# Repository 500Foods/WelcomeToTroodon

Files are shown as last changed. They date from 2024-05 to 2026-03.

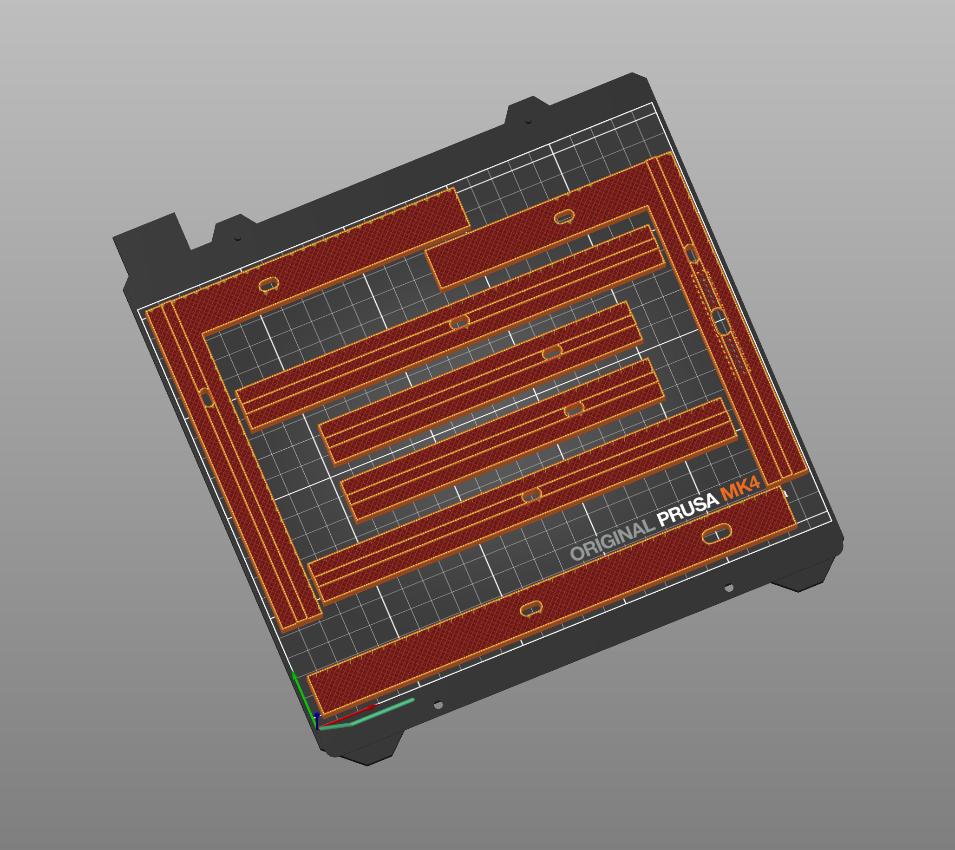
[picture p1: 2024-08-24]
3D_Files/RearPanelInserts/RearPanelInserts-01.png

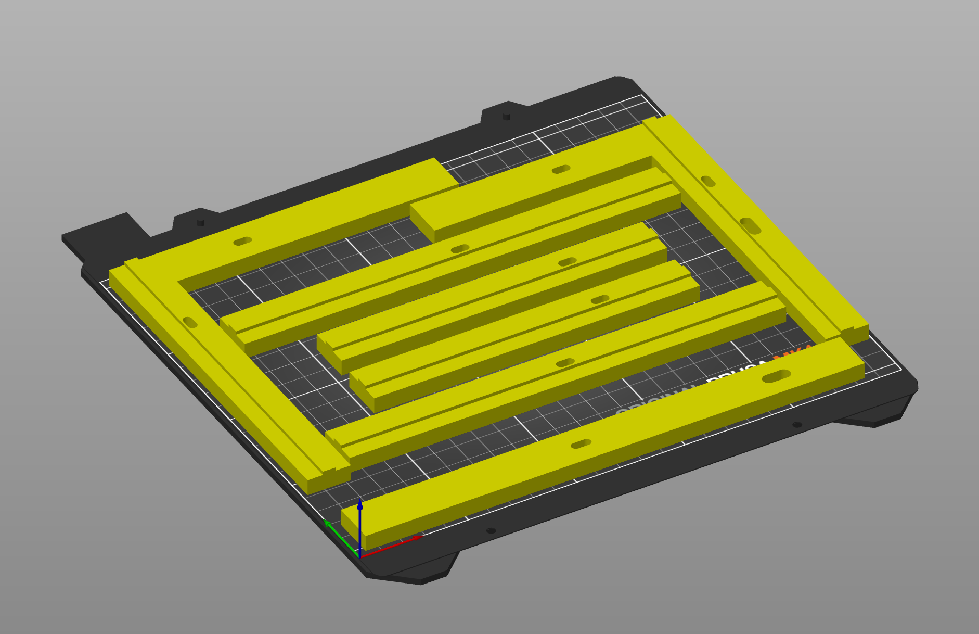
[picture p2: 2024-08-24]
3D_Files/RearPanelInserts/RearPanelInserts-00.png

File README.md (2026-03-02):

# Welcome To Troodon
This repository has been created primarily as a community resource for those with a new [Troodon 3D printer](https://www.formbot3d.com/collections/troodon-390). Troodons are very close relatives of the popular Voron series of printers. A great deal of the content here applies equally to those printers, as well as many other 3D printers. 

Note: This is a new project with many pages yet to be completed.

%20Completed%20&width=415&suffix=%20%2F%20111%20Pages"

## 📚 Where to Start
- [🤔 Getting Started Resources](https://github.com/500Foods/WelcomeToTroodon/blob/main/docs/getting_started.md) - Documentation, assembly guides, and more
- [🤓 Effort, Expertise, and Expense](https://github.com/500Foods/WelcomeToTroodon/blob/main/docs/effort.md) - Just a note that each person's journey is unique
- [🧐 Fussy Filaments](https://github.com/500Foods/WelcomeToTroodon/blob/main/docs/filaments.md) - Get the most out of the filaments you want to use
- [⚠️ Initial Build Tips](https://github.com/500Foods/WelcomeToTroodon/blob/main/docs/initial_build.md) - Getting your printer printing is job #1

## 🚀 Next Steps
- [🙂 Level One - Welcome!](https://github.com/500Foods/WelcomeToTroodon/blob/main/docs/level_1.md) - Get on a solid footing with the stock configuration 
- [🔨 Level Two - Get to Work!](https://github.com/500Foods/WelcomeToTroodon/blob/main/docs/level_2.md) - Updates and mods you'll want to implement as soon as possible
- [🥇 Level Three - More Speed!](https://github.com/500Foods/WelcomeToTroodon/blob/main/docs/level_3.md) - For when you want to push your printer to its limits
- [⏰ Routine Maintenance](https://github.com/500Foods/WelcomeToTroodon/blob/main/docs/maintenance.md) - What to keep an eye on to avoid nasty surprises

## 🏹 Quick Reference
- [🪜 HowTo's](https://github.com/500Foods/WelcomeToTroodon/blob/main/docs/level_h/README.md) - Assorted step-by-step guides
- [🪛 Configs](https://github.com/500Foods/WelcomeToTroodon/blob/main/docs/configuration.md) - Get the most from Klipper's printer.cfg
- [✂️ Macros](https://github.com/500Foods/WelcomeToTroodon/blob/main/docs/macros.md) - Klipper macros like PRINT_START
- [⚔️ Slicers](https://github.com/500Foods/WelcomeToTroodon/blob/main/docs/slicers.md) - Settings for Orca Slicer and others
- [🪚 Scripts](https://github.com/500Foods/WelcomeToTroodon/blob/main/docs/scripts.md) - Bash scripts integrated with Klipper

## 🎪 More to Explore
- [🥳 Showcase](https://github.com/500Foods/WelcomeToTroodon/blob/main/docs/showcase.md) - Tell us about your printer or what you've printed
- [💣 Experimental Projects](https://github.com/500Foods/WelcomeToTroodon/blob/main/docs/experiments.md) - Ideas that aren't quite fully baked yet

<p><br></p>

## 📏 Repository Information &nbsp; &nbsp; &nbsp; &nbsp; 
<!--CLOC-START -->
```
Last updated at 2026-03-02 03:53:08 UTC
-------------------------------------------------------------------------------
Language                     files          blank        comment           code
-------------------------------------------------------------------------------
Markdown                       114            634              2           2804
YAML                             1              8             13             35
Bourne Shell                     4              6             39             19
-------------------------------------------------------------------------------
SUM:                           119            648             54           2858
-------------------------------------------------------------------------------
9 Files were skipped (duplicate, binary, or without source code):
  3mf: 5
  png: 2
  cfg: 1
  stl: 1
```
<!--CLOC-END-->

<p><br></p>

## 💡 Contributions Encouraged
If you see something that could be improved, or if you have ideas for additional content, please create a GitHub Issue here in this repository, submit a GitHub PR directly if you're so inclined, or reach out to @500Foods on the #troodon_2 channel in the [FormBot Discord](https://discord.gg/spAGFK2PnN).

This project is still at a very early stage, so there are plenty of blank pages waiting to be populated. If you run across one of those and would like to help out, please get in touch.

If you find this work interesting, helpful, or valuable, or that it has saved you time, money, or both, please consider directly supporting these efforts financially via [GitHub Sponsors](https://github.com/sponsors/500Foods) or donating via [Buy Me a Pizza](https://www.buymeacoffee.com/andrewsimard500).

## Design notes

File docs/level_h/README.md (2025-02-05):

# HOWTO Guides Quick Reference

Here is a list of guides for performing common modifications or supplemental builds for your 3D printer. Some are specific to Troodon, as noted, and some are suitable for any 3D printer. 

## Specific to the Troodon 2.0 Pro 
- [BTT Sensor](https://github.com/500Foods/WelcomeToTroodon/blob/main/docs/level_h/btt_sensor.md) - Install the BTT Smart Filament Sensor as an alternative to the stock filament runout sensor.
- [Rockers](https://github.com/500Foods/WelcomeToTroodon/blob/main/docs/level_h/rockers.md) - Make it easier to get into the electronics bay
- Chamber Lighting - Dramatically better lighting option
- Install a 5V Buck Converter - Add a 5V power source to run LEDs

## Applicable to any modern Klipper-based 3D printer
- [Install KIAUH and DangerKlipper](https://github.com/500Foods/WelcomeToTroodon/blob/main/docs/level_h/KIAUH_danger.md) - Get the latest Klipper release and a tool to manage it
- Build a TradRack MMU - Add multi-color or multi-material capabilities to your printer
- Klipper Expander - Add more IO to your Klipper-based printer
- Audio Upgrade - Get your printer talking
- KNOMI Remote - Setup KNOMI as a desk accessory

## References
- [KIAUH](https://github.com/dw-0/kiauh) - Klipper Installation and Update Helper
- [DangerKlipper](https://github.com/DangerKlippers/danger-klipper) - The "risky" fork of Klipper with additional features

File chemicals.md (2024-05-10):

# Chemicals
- Glass Cleaner
- Pure Isopropyl Alcohol
- Pure Acetone
- Bed Adhesive

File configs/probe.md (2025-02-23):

# [probe]
This is used to configure the Voron TAP probe found on Troodon printers and others. If you've got a different probe, then by all means follow the documentation and disregard these settings.

The TAP probe uses the nozzle directly, so the x_offset and y_offset are both set to zero.

Note that the TAP probe is used in both the Quad Gantry Levelling process as well as the Bed Mesh Levelling process. When making changes here, please be sure to test those as well.

***NOTE: In some printer.cfg files like the stock Troodn 2.0 Pro shipping configs, there's a left-over "activate g-code" bit that should be removed.***

***NOTE: Setting z_offset as suggested in the documentation seems to set it globally, meaning that it changes the z_offset for your printer. Which is absolutely not what is intended. So this value is deliberately not included here. I've got a wonderfully engraved first layer in a glass bed as a testament to this.***

```
#####################################################################
# Voron TAP config (probe IS the nozzle)
#####################################################################
[probe]
pin: PF4

x_offset: 0    # Distance between the probe and the nozzle in mm
y_offset: 0    # Distance between the probe and the nozzle in mm

speed: 10.0                     # z-axis speed when probing (max=10 mm/s)
lift_speed: 100.0               # z-axis lift speed when probing (max=100 mm/s)

samples: 3                      # Number of times to probe each point
samples_result: average         # Median or average calculation for multiple samples
samples_tolerance: 0.005        # Maximum tolerance between probe values
samples_tolerance_retries: 10   # Number of times to retry before giving up
sample_retract_dist: 2.0        # Distance to lift between each probe (mm)
```

## References
- [Voron TAP GitHub Repository](https://github.com/VoronDesign/Voron-Tap) - Software and links to CAD drawings, etc.
- [Voron TAP Assembly Manual](https://github.com/VoronDesign/Voron-Tap/blob/main/Manual/Assembly_Manual_Tap.pdf) - If you want to assemble or repair the Voron TAP probe
- [Klipper TAP Documentation ](https://www.klipper3d.org/Config_Reference.html#probe)- List of parameters

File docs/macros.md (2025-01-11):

# ✂️ Quick Reference - Macros
Macros are typically defined in the printer.cfg file. Some of these macros may already present - particularly PRINT_START and PRINT_END. Be sure to comment out any existing macro while testing changes, so you can revert back to the prior version if you encounter any problems.
- [HEAT_SOAK](https://github.com/500Foods/WelcomeToTroodon/blob/main/macros/HEAT_SOAK.md) - Heat soak the printer for more consistent prints
- [LIGHTS_TOGGLE](https://github.com/500Foods/WelcomeToTroodon/blob/main/macros/LIGHTS_TOGGLE.md) - Turn the main chamber light on or off via a macro or a KlipperScreen button
- [PRINT_START](https://github.com/500Foods/WelcomeToTroodon/blob/main/macros/PRINT_START.md) - Runs whenever a new print job is sent to the printer
- [PRINT_CANCEL](https://github.com/500Foods/WelcomeToTroodon/blob/main/macros/PRINT_CANCEL.md) - Runs whenever a new print job is canceled, manually or otherwise
- [TIMER](https://github.com/500Foods/WelcomeToTroodon/blob/main/macros/TIMER.md) - Adds support for adding timers to other macros, particularly to PRINT_START
- [TEMPS](https://github.com/500Foods/WelcomeToTroodon/blob/main/macros/TEMPS.md) - Change how Klipper monitors temperatures to more of a "temp reached" rather than "temp stable" mode

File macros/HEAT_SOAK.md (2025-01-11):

# HEAT_SOAK
For some filaments, like ASA or ABS, it is helpful to have the printer set up with as high a chamber temperature as possible. Naturally this applies to enclosed printers only.
In addition, it helps if the printer is at that temperature for a period of time so that all of the compnents also reach the same temperature.
This is known as "heat soaking" the printer, and generally leads to improved (aka more consistent) prints. Particularly compared to starting the printer cold.

Discord #troodon_2 user @Chase has provided the following macros for just this purpose. Using the UI, the desired temperature and duration can be set. 
For a stock Troodon 2.0 Pro, a chamber temperature of 40C for 20 minutes would be a good place to start.



```
[gcode_macro HEAT_SOAK]
description: heats the bed for a while

variable_target_temp: 0
variable_stage: None ## heating -> soaking -> done -> None

## in seconds
variable_check_interval: 10
variable_soak_time_remaining: 0
variable_total_time_elapsed: 0

gcode:
    {% set TARGET = params.TARGET | default(0) | float %}
    {% set DURATION = (params.DURATION | default(5) | int) * 60 %} ## minutes to seconds

    SET_GCODE_VARIABLE MACRO=HEAT_SOAK VARIABLE=target_temp         VALUE={ TARGET }
    SET_GCODE_VARIABLE MACRO=HEAT_SOAK VARIABLE=stage               VALUE="'heating'"
    SET_GCODE_VARIABLE MACRO=HEAT_SOAK VARIABLE=soak_time_remaining VALUE={ DURATION }
    SET_GCODE_VARIABLE MACRO=HEAT_SOAK VARIABLE=total_time_elapsed  VALUE=0

    ;; fire up the heater
    SET_HEATER_TEMPERATURE HEATER=heater_bed TARGET={ TARGET }

    ;; run the parts fan to circulate air
    M106 S255

    ;; put the bed and nozzle where they're a safe distance apart
    G28

    M84 ;; turn off steppers

    UPDATE_DELAYED_GCODE ID=heat_soaker DURATION={ check_interval }

[gcode_macro CANCEL_HEAT_SOAK]
description: cancels an in-progress HEAT_SOAK cycle
gcode:
    SET_GCODE_VARIABLE MACRO=HEAT_SOAK VARIABLE=stage VALUE="'cancel'"
    UPDATE_DELAYED_GCODE ID=heat_soaker DURATION=1

[delayed_gcode heat_soaker]
; ## debug
; { action_respond_info( printer['gcode_macro HEAT_SOAK'] | tojson )}
gcode:
    {% set heat_soak = printer['gcode_macro HEAT_SOAK'] %}

    ## update total time elapsed
    {% set total_time_elapsed = heat_soak.total_time_elapsed + heat_soak.check_interval %}
    SET_GCODE_VARIABLE MACRO=HEAT_SOAK VARIABLE=total_time_elapsed VALUE={ total_time_elapsed }

    {% set stage = heat_soak.stage %}
    {% if stage == "heating" and printer.heater_bed.temperature >= heat_soak.target_temp %}
        {% set stage = "soaking" %}
    {% endif %}

    {% if stage == "soaking" %}
        ## update soak countdown
        {% set soak_time_remaining = [heat_soak.soak_time_remaining - heat_soak.check_interval, 0] | max %}
        SET_GCODE_VARIABLE MACRO=HEAT_SOAK VARIABLE=soak_time_remaining VALUE={ soak_time_remaining }

        {% if soak_time_remaining == 0 %}
            {% set stage = "done" %}
        {% endif %}
    {% endif %}

    SET_GCODE_VARIABLE MACRO=HEAT_SOAK VARIABLE=stage VALUE="'{ stage }'"

    {% if stage in ("done", "cancel") %}

        {% if stage == "cancel" %}
            {% set stage = "done" %}
            TURN_OFF_HEATERS
            M107 ; turn off fan

            M117 { "soak cancelled after ~%.1fm" | format(total_time_elapsed / 60.0) }
        {% else %}
            M117 { "soak complete after %.1fm" | format(total_time_elapsed / 60.0) }
        {% endif %}

        ## reset all state vars, except stage, which may be queried via the api
        SET_GCODE_VARIABLE MACRO=HEAT_SOAK VARIABLE=target_temp         VALUE=0
        SET_GCODE_VARIABLE MACRO=HEAT_SOAK VARIABLE=soak_time_remaining VALUE=0
        SET_GCODE_VARIABLE MACRO=HEAT_SOAK VARIABLE=total_time_elapsed  VALUE=0

    {% else %}

        {% if total_time_elapsed % 90 == 0 %}
            ## output status periodically
            {% if stage == "heating" %}
                M117 { "heating -- %.1fm elapsed" | format(total_time_elapsed / 60.0) }
            {% elif stage == "soaking" %}
                M117 { "soaking -- %.1fm remaining" | format(soak_time_remaining / 60.0) }
            {% endif %}
        {% endif %}

        ## trigger ourselves again
        UPDATE_DELAYED_GCODE ID=heat_soaker DURATION={ heat_soak.check_interval }

        ## dwell for 1ms to prevent from going idle
        G4 P1

    {% endif %}
```
#

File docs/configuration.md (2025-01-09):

# 🪛 Quick Reference - Configuration
Configuration items are typically defined in the printer.cfg file. Be careful with these customizations as the hardware in your printer may be very different than what is assumed here. 

***Note: Any changes to Klipper's printer.cfg file will require a reboot to take effect.***

***Note: Before copying and replacing large sections of a printer.cfg file, be mindful that there is typically a printer-specific serial number appearing near the beginning of the file. 
This is tied to the serial number of the MCU board (an Octopus F407 board in the case of the Troodon 2.0 Pro). Be careful not to overwrite that line.***

- printer.cfg [[exclude_object]](https://github.com/500Foods/WelcomeToTroodon/blob/main/configs/exclude_object.md) - Enable option for excluding failed objects from the currently running print job
- printer.cfg [[gcode_arcs]](https://github.com/500Foods/WelcomeToTroodon/blob/main/configs/gcode_arcs.md) - Enable support for G2/G3 G-Code commands
- printer.cfg [[probe]](https://github.com/500Foods/WelcomeToTroodon/blob/main/configs/probe.md) - Voron TAP optimizations
- printer.cfg [[quad_gantry_level]](https://github.com/500Foods/WelcomeToTroodon/blob/main/configs/qgl.md) - Improve the QGL process
- printer.cfg [[fan]](https://github.com/500Foods/WelcomeToTroodon/blob/main/configs/fans.md) - View more fan data, control fans directly

## Troodon Configurations from Discord #troodon_2 users
- [@Don_Duce](https://github.com/donduce/Troodon-2.0-Pro-350mm) - Clean setup, with macros.cfg separated out, suitable for stock Troodon 2.0 Pro with SB + TAP

## Stock Configuration Files
- [Stock Troodon printer.cfg](https://github.com/YGK3D/Troodon-2-Klipper/blob/main/Troodon2-Klipper-YGK3D-v1_2-printer.cfg) - Version 1.2 Released 02/09/23 (before TAP was added to stock)
- [Stock Troodon printer.cfg - 2024 Edition](https://github.com/500Foods/WelcomeToTroodon/blob/main/docs/original_troodon_2.0_pro_with_tap_printer.cfg) - This is the version shipped with CNC TAP machines
#
Next: [Quick Reference - Macros](https://github.com/500Foods/WelcomeToTroodon/blob/main/docs/macros.md)

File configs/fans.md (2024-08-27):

# Fans
There are numerous fans running inside of a typical modern 3D printer. Some of them are critical - a failure of the fan could result in damage to the printer. Or worse. 
Some of them are necessary - a failure could lead to an unsuccessful print. 
And some of them are just nice to have - speeding up print times or reducing the noxious fumes emanating from the printer when printing with certain filaments like ABS or ASA.

There are of course different sizes and styles of fans with distinct performance characteristics. Some fans are really small, just big enough to get air flowing over a chip to keep it cool, as is the case with fans on the printer toolhead.
Chamber exhaust fans, on the other hand, are intended to move a much larger volume of air through an activated carbon filter, and as they are mounted on the enclosure, they can be much larger, spin more slowly, and thus be much quieter.
Part-cooling fans get most of the attention. These are generally high-performance fans - blowers, typically - designed specifically to maximize airflow over the part so that it can be cooled before the next layer comes around. 
High-speed PLA printing requires part-cooling fans, with an almost unlimited need for more airflow. When printing ABS or ASA on the other hand, the part-cooling fan is almost unnecessary.

Communicating with fans, what we're primarily interested in here, can take many forms as well. Some fans just run when the printer has power - no communication of any kind. Some can be turned on or off, but run at a set speed. 
Some can have their speed set manually or controlled automatically based on a related heater or thermistor output. And, the most rare, some can report their speeds using a built-in tachometer so you can see exactly how fast they are spinning or if indeed they are spinning at all.

One clue as to whether a fan has these extra capabilities can be found in the number of pins or wires running to the fan. 2-pin fans might be of the on/off variety, but using PWM (pulse width modulation), some fans can be controlled by quickly cycling the voltage to the fan. 
A 3-pin fan might use the third pin for this PWM function, whereas using just the first two pins would convert it to an on/off style fan. Some 3-pin fans use the third pin as the tachometer. And then there are 4-pin fans with separate PWM and tach pins. And, for all of these,
fans can run at 5V, 12V, or 24V. 3D printers tend to use 24V, or in a pinch, 5V.

As with all the parts of a typical printer, there are cheap fans and expensive fans. And, for the most part, printers ship with fans that work well enough for the print jobs the printer was designed for. 
But they are also good candidates for upgrading when more performance is required, or even when more fans are needed. The main differentiators, aside from the physical size, pins, and voltage, relate to the amount of airflow, usually advertised in CFM, the amount of noise generated, 
measured in dB, and the maximum power draw, in amps. 

## Klipper [fan] sections
Within Klipper's printer.cfg, there will be a section for each fan that Klipper knows about, and this [fan] section will determine to some degree how the fan works within the rest of the Klipper environment. 
Naturally, the configuration for the fan has to match the hardware characteristics of the fan. If you're using a 2-pin fan, it is unlikely that you'll be able to get a tachometer reading from it, for example, no matter how much you'd like to see one. 
Also, just because a fan hasn't been listed in printer.cfg doesn't mean that it can't be added. The fan on an MCU or CPU (or both!) are good candidates to add to printer.cfg if they're already there. 
Likewise, just because a fan has been configured a certain way by default doesn't mean that you can't change it to work a different way.

The main complication with [fan] configuration comes up when you want the fan to be controlled automatically by something else. For example, turning on a particular fan when a heater is turned on, for example. We'll see some examples of this in the sections below.
As usual, refer to the [Klipper Documentation - Fans](https://www.klipper3d.org/Config_Reference.html#fans) for the latest information on how to configure even the most complex fan arrangement.

## [fan_generic] Exhaust Fan
Sometimes referred to as the chamber fan, this is typically the fan at the back of the printer that draws air out of the chamber and pushes it through an activated carbon filter. Why activated carbon? 
Well, the VOCs that are created when printing with filaments like ABS or ASA are too small for a HEPA filter to catch. We're calling it the exhaust fan here because "chamber fan" describes another kind of fan discussed below.

***Note: Activated carbon doesn't last all that long, so if you're finding that your printer is a little more unpleasant to spend time around than normal, it might be a good idea to consider replacing the activated carbon filter.***

On a Troodon 2.0 Pro, this is a 60mm x 60mm x 20mm 24V 2-pin PWM fan. Which means we can control the speed, but we can't tell how quickly it is spinning. In the default Troodon printer.cfg, this fan is configured to turn on automatically when the bed heater rises above 60C.
In this automated configuration, there's no way to set the exhaust fan speed, either through the UI or through any other means - it just does what it's told. 
And as this is done in Klipper.cfg, this means that the configuration (and thus the fan speed) cannot be changed without restarting Klipper. Not so fun.

```
##  Exhaust fan - FAN3
[heater_fan exhaust_fan]
pin: PE5
max_power: 1.0
shutdown_speed: 0.0
kick_start_time: 5.0
heater: heater_bed
heater_temp: 60
fan_speed: 1.0
```
Let's instead change this configuration to use a different Klipper fan mode - moving from [heater_fan] to [fan_generic]. In this mode, the fan shows up in the Klipper UI with a slider to control the speed as a percentage.
```
##  Exhaust fan - FAN3
[fan_generic exhaust_fan]
pin: PE5
max_power: 0.7
shutdown_speed: 0.0
kick_start_time: 5.0
```
As an added benefit, we can also control this fan now using G-code macros. Perhaps we want to change the exhaust fan speed at different points in a print. 

For example, when printing with ABS or ASA, we generally want the exhaust fan speed to be low, around 30% or so, so that a high chamber temperature can be maintained, but still filter the air slowly. 
But when the print is done, we want the chamber to cool down more quickly, and filtering as much of the air as possible becomes the priority. with [fan_generic] fans, we can just set the fan speed directly.
```
[PRINT_START]
...
    # Exhaust fan to low (Note: Requires [fan_generic exhaust_fan] configured)
    SET_FAN_SPEED FAN=exhaust_fan SPEED=0.3  # Exhaust fan to low -> don't want to cool the chamber 
...

[PRINT_END]
...
    # Exhaust fan to max (Note: Requires [fan_generic exhaust_fan] configured)
    SET_FAN_SPEED FAN=exhaust_fan SPEED=1.0  # Exhaust fan to max -> cool chamber fast
...
```

## [controller_fan] MCU and CPU Fans
These are auxiliary fans that are attached, respectively, to the MCU and the CPU and will vary from printer to printer.

In addition to being able to control these fans, we'd also like to know something about what they are attached to.
So in these instances, we're also interested in Klipper [[temperature_sensor]](https://www.klipper3d.org/Config_Reference.html#builtin-micro-controller-temperature-sensor) sections. 

For our typical Troodon printer, this might look like the following. Note that the min_temp and max_temp values are hard limits. If they are exceeded, Klipper will abruptly shutdown. 
And that only the MCU fan is controlled here - simply turned on whenever the heater_bed is turned on, which is almost always the case when printing nearly anything.

```
##  Controller fan - FAN2
[controller_fan octopus_controller_fan]
pin: PC6
kick_start_time: 0.5
heater: heater_bed

#####################################################################
#   Host CPU Temperature
#####################################################################
[temperature_sensor BTT-CB1]
sensor_type: temperature_host
min_temp: 0
max_temp: 100

#####################################################################
#   Controller MCU Temperature
#####################################################################
[temperature_sensor Octopus]
sensor_type: temperature_mcu
min_temp: 0
max_temp: 100
```
With these in place, the MCU and CPU temperatures will be included in the Klipper temperature graph, and the MCU fan will be listed among the other fans, showing whether or not it is running.

## [temperature_fan] Supplemental CPU Fan
While the stock Troodon doesn't come with a fan attached to the BTT-CB1 (a Raspberry Pi clone) - it just uses a heatsink - it is possible to add a fan to the heatsink.
And there's a convenient fan header pin positioned right beside the heatsink as well, making this an easy process, as demostrated here by user @Don_Duce in the Formbot Discord #Troodon_2 channel:

<br/>
*Custom fan added to BTT-CB1*

Then, to enable this fan, another Klipper [fan] section can be added where the pin definition comes from the [BTT-Pi repository](https://github.com/bigtreetech/BTT-Pi/blob/master/BIGTREETECH%20Pi%20V1.2%20-%20Board%20Fan%20Pin%20Configuration).
In this case, the fan is temperature-controlled, meaning that a temperature sensor is used to control the fan. Conveniently, we've just added the sensor we need as `temperature_host` so the config looks something like this.
The extra PID parameters are used to adjust the fan speed as the temperature rises.
```
[temperature_fan btt_cb1_fan]
sensor_type: temperature_host
pin: host:gpio211
kick_start_time: 0.8
max_power: 1.0
control: pid
min_temp: 0
max_temp: 85
pid_kp: 1.0
pid_ki: 0.5
pid_kd: 2.0
min_speed: 0.1
max_speed: 0.6
target_temp: 38
```

## [heater_fan] Hotend Fan
Here we're referring to the fan that is in the toolhead. Normally, this will be running at 100% whenever the extruder heater is on. 
This is a critical fan, as without it the heat from the heat block will slowly creep up into the extruder and start melting things that are not supposed to be melted.
The unchecked failure of this fan will likely result in having to only replace parts of the toolhead, if you're lucky enough to catch it in time.

```
##  Hotend Fan - FAN1
[heater_fan hotend_fan]
pin: PB8
max_power: 1.0
kick_start_time: 0.5
heater: extruder
heater_temp: 50.0
##  If you are experiencing back flow, you can reduce fan_speed
#fan_speed: 1.0
```
Generally speaking, this is going to turn on to 100% as soon as the toolhead heater (the extruder in Klipper's terms) turns on, and will remain at 100% so long as that heater is running.
It isn't a very large or noisy fan, so this isn't likely to be of concern. What is of concern is paying attention to whether it is working or not. If your extruder starts doing odd things,
like not being able to maintain consistent temperatures, having a quick check to ensure this fan is working would be at the very top of the list. Just takes a bit of debris to get jammed
into the fan to have it stop working, with a melted toolhead as the result.

## [fan] Part-Cooling Fan
This is the fan (or perhaps more than one) that tends to get all the attention, and why it is listed as [fan] without any kind of qualifier. Perhaps in some of the earliest 3D printers.
this was the only fan that could be controlled, or needed to be controlled. 
```
#  Print Cooling Fan - FAN0
[fan] 
pin: PB7
kick_start_time: 0.5
##  Depending on your fan, you may need to increase this value
##  if your fan will not start. Can change cycle_time (increase)
##  if your fan is not able to slow down effectively
off_below: 0.10
```
The use of this fan isn't really something that is managed in Klipper's printer.cfg because it most often is controlled more precisely by the G-code for the print job. 
As a print progresses through different layers, the speed of this fan is often adjusted to compensate for various issues. Overhangs and bridging might require more aggressive cooling, 
as would very short layer times. On the other hand, if it is a big print job and the layer times are really long at various points, then the part-cooling requirements are reduced.

## [temperature_fan] Chamber Fan
The final Klipper [fan] mode is one that isn't defined in a stock Troodon configuration, but would likely appear in one that has been upgraded to have chamber fans, or if a supplemental
CPU fan is added like we showed above.
What are chamber fans? These are auxiliary fans, like nevermore or The Fan, that circulate air within the chamber, typically through their own additional activated carbon filters.
Why? Two primary reasons. More VOC filtering and higher chamber temperatures.

For the VOC side, having an in-chamber fan/filter combination allows the air inside the chamber to pass through the activated carbon filter potentially many times before exiting via the exhaust fan.
This can dramatically reduce the VOCs present in the exhaust. Having several such fans/filters in the chamber can multiply this even further. Projects like nevermore and The Fan support two, three,
or even four in-chamber fans.

For the chamber temperature issue, the goal is to incease the overall chamber temperature to around 50C - 60C when printing with filaments like ABS or ASA. This higher chamber temperature helps to
reduce the warping that can occur with these filaments, as the change in temperature between the already printed component of the print and the new plastic laid down on top is significantly reduced.
And this is what causes the warping in the first place. The higher layers are laid down at a cooler temperature, so they shrink a little more, pulling up on the corners, causing the print to warp.

There are other considerations, like having a fully enclosed and properly sealed chamber to begin with. As well as having accurate chamber thermistors. And that's where the [temperature_fan] part comes in - by monitoring the 
chamber temperature, these fans, typically placed under the heated bed, distribute the heat from the bed heater to the rest of the printer. This greatly reduces the time needed to get the chamber
to the desired temperature, and also for heat-soaking the printer, where that temperature is maintained for a short time (say, 20 minutes) before printing begins.

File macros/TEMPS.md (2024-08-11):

# TEMPS
Sometimes it can take a while for Klipper to "accept" that a new temperature has been reached, either for the extruder temperature or the bed heater temperature. 
It tries to wait for the temperature to "stabilize" but in some instances, that stabilization takes a long time, or might not even be reached. This is particularly the case when using faster heaters or if the PID calibration hasn't been performed recently.

To get around this, and to make the whole process quicker, Klipper can be configured to instead simply wait for the temperature to be reached, rather than to be stabilized. This is achieved by replacing Klipper macros with different versions.

```
[gcode_macro M109]
rename_existing: M99109
gcode:
    #Parameters
    {% set s = params.S|float %}
    
    M104 {% for p in params %}{'%s%s' % (p, params[p])}{% endfor %}  ; Set hotend temp
    {% if s != 0 %}
        TEMPERATURE_WAIT SENSOR=extruder MINIMUM={s} MAXIMUM={s+1}   ; Wait for hotend temp (within 1 degree)
    {% endif %}

[gcode_macro M190]
rename_existing: M99190
gcode:
    #Parameters
    {% set s = params.S|float %}

    M140 {% for p in params %}{'%s%s' % (p, params[p])}{% endfor %}   ; Set bed temp
    {% if s != 0 %}
        TEMPERATURE_WAIT SENSOR=heater_bed MINIMUM={s} MAXIMUM={s+1}  ; Wait for bed temp (within 1 degree)
    {% endif %}
```
# Reference
- Ellis' Print Tuning Guide - [Replace M109/M190 With TEMPERATURE_WAIT](https://ellis3dp.com/Print-Tuning-Guide/articles/useful_macros/replace_m109_m190_with_temp_wait.html)

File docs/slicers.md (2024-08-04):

# ⚔️ Slicers Quick Reference
Popular slicer software like Orca Slicer will generally work pretty well out of the box, as it comes with presets for a vast array of printers, including Troodon printers. There's always room for improvement though.
- [Orca Slicer](https://github.com/500Foods/WelcomeToTroodon/blob/main/configs/orca.md) - Check that Klipper is being supplied with as much information as it can from Orca Slicer

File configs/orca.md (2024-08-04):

# Orca Slicer
Depending on how a printer was originally configured in Orca, there may be a lot of information sent along with the G-code to Klipper, or there may be very little. 
And within Orca's normal settings, there are options to be more or less verbose when generating G-code. 
These are all things to be aware of if you're trying to get data into your Klipper macros or even over to Linux Bash scripts using the gcode_shell_command extension.
There are also features within Klipper that won't work properly without support enabled in Orca.

Note: These screenshots are from Orca 2.1 (beta) running under Fedora. 

## G-code Labels
If you routinely send prints with multiple objects, a recent Klilpper update provides a mechanism to exclude objects individually. This can be helpful if one of them gets knocked out of position or fails in some other way. 
If you've got a plate full of objects, this allows the print to continue along and complete the rest of the objects. Very handy. But in order for it to work, the objects need to be labeled in G-code. This setting can be
found on the 'Others' tab when the Advanced option is enabled.



## Machine start G-code
This is code that Orca includes in the G-code sent to the printer at the beginning of every print. The parameters we're expecting in our [PRINT_START] macro are provided by this mechanism. This can be found under the main
printer settings in the Machine G-code tab.



In this case, the PRINT_START macro is called with the temperature values chosen for EXTRUDER and BED being passed to it. These will have come from Orca settings, typically linked to the choice of filament being used.

In the second line, an extra value is passed - the total number of layers in the print job. This makes the value available to Klipper macros, in case you want to use some kind of progress calculation or pass this value out to a Linux Bash script.
```
PRINT_START EXTRUDER=[nozzle_temperature_initial_layer] BED=[bed_temperature_initial_layer_single]
SET_PRINT_STATS_INFO TOTAL_LAYER=[total_layer_count]
```

## Layer change G-code
Scrolling down the Machine G-code tab a little further, there is this section which is inserted into the G-code whenever the slicer moves to a new layer. If you're using the Timelapse module with Klipper, you'll already
have the function call to trigger that module to generate a new image. 



In this case, in addition to the Timelapse call, there's another Klipper mechanism to set the value for the current layer. As before, this makes it possible to do things in Klipper related to progress or to kick off something
when certain layers are achieved. Perhaps a fan or heater can be turned on or off once a few layers have been laid down, or different lighting modes can be enabled as the print progresses through 25%, 50%, and so on.
```
;AFTER_LAYER_CHANGE
;[layer_z]
SET_PRINT_STATS_INFO CURRENT_LAYER={layer_num + 1} 
TIMELAPSE_TAKE_FRAME
```
Note: lines beginning with a ; will still be inserted into the G-code, which you can see in the slicer output. But they aren't executed or visible to Klipper macros.

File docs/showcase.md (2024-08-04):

# 🥳 Showcase
Have you printed something amazing? Or complicated? Or Unusual? Or maybe something failed? We'd like to see those as well.

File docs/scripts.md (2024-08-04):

# 🪚 Scripts Quick Reference
Typically these would be installed in ~/scripts on the BTT-CB1 or Raspberry Pi or wherever Klipper is running. Some of the scripts are intended for use with the [gcode_shell_command](https://github.com/dw-0/kiauh/blob/master/docs/gcode_shell_command.md) extension that can be very easily installed using [KIAUH](https://github.com/dw-0/kiauh). As its name implies, this extension allows for running Linux shell commands directly as gcode commands within, for example, printer.cfg. Rather useful. Note that most interfaces to the Klipper log allow you to filter entries, which comes in handy here in particular. 
Note also that Linux scripts can be written in multiple languages, but most commonly Bash and Python in this environment.

- ### [Time and Timer Shell Scripts](https://github.com/500Foods/WelcomeToTroodon/blob/main/docs/level_s/time_timer.md)
  - [get_current_datetime.sh](https://github.com/500Foods/WelcomeToTroodon/blob/main/scripts/get_current_datetime.sh) - Output the current date/time in Klipper logs in ISO8601 format
  - [log_current_datetime.sh](https://github.com/500Foods/WelcomeToTroodon/blob/main/scripts/log_current_datetime.sh) - Start a timer within Klipper
  - [get_elapsed_time.sh](https://github.com/500Foods/WelcomeToTroodon/blob/main/scripts/get_elapsed_time.sh) - Show the elapsed time

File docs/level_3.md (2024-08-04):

# 🥇 Level Three - More Speed!  
Once everything is up and running smoothly, your gaze will quickly turn toward faster print speeds. No end to the available options here. Let's have a look at some of the most popular and effective options in these categories.

- 🥇 [CAN Bus](https://github.com/500Foods/WelcomeToTroodon/blob/main/docs/level_3/canbus.md) - Greatly simplify the wiring in your printer
- 🥇 [Umbilicals](https://github.com/500Foods/WelcomeToTroodon/blob/main/docs/level_3/umbilicals.md) - A different cable path option
- 🥇 [Extruders](https://github.com/500Foods/WelcomeToTroodon/blob/main/docs/level_3/extruders.md) - Simpler - Lighter - Stronger - Lots of options
- 🔨 [Hotends](https://github.com/500Foods/WelcomeToTroodon/blob/main/docs/level_3/hotends.md) - Increased filament flow is the primary objective here
- 🔨 [Cooling](https://github.com/500Foods/WelcomeToTroodon/blob/main/docs/level_3/cooling.md) - High-speed printing often calls for high-speed cooling
- 🥇 [Controller Boards](https://github.com/500Foods/WelcomeToTroodon/blob/main/docs/level_3/controllers.md) - No shortage of options here
- 🥇 [Computer Boards](https://github.com/500Foods/WelcomeToTroodon/blob/main/docs/level_3/computer.md) - When your printer needs to do a little more than just print

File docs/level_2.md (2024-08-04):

# 🔨 Level Two - Get to Work!
This list is aimed at those who might be planning for a more production-oriented environment. Maybe you're using your printer in a business. Maybe you have an Etsy store. Maybe you print a lot of the same things over and over again. Or maybe you just like to tinker. Here are modifications that can help ensure reliable prints day in and day out. And again, we're not touching anything in the main filament path of the printer but instead focused on everything around it. Often, small updates or modifications can make a big difference in the day-to-day experience. These are intended to be on the less expensive and easy-to-implement side of the fence, accessible to most everyone without too much of a learning curve.

- 🙂 [Drop-in HotEnd Replacements](https://github.com/500Foods/WelcomeToTroodon/blob/main/docs/level_2/hotends.md) - A quick way to get more performance from your printer
- 🔨 [TAP Upgrades](https://github.com/500Foods/WelcomeToTroodon/blob/main/docs/level_2/tap_upgrades.md) - Replace the plastic TAP mount with a metal CNC part
- 🥇 [TAP Alternatives](https://github.com/500Foods/WelcomeToTroodon/blob/main/docs/level_2/tap_alternatives.md) - Upgrade to an entirely different bed mesh sensor
- 🙂 [Alternative Build Plates](https://github.com/500Foods/WelcomeToTroodon/blob/main/docs/level_2/build_plates.md) - Explore different print surfaces
- 🙂 [Chamber Fans and Filters](https://github.com/500Foods/WelcomeToTroodon/blob/main/docs/level_2/chamber_fans.md) - Upgrade VOC filtering, higher chamber temperatures
- 🔨 [Chamber Lighting](https://github.com/500Foods/WelcomeToTroodon/blob/main/docs/level_2/chamber_lighting.md) - Improve the lighting for better visibility, timelapse videos, etc.
- 🥇 [Multi-material and Multi-Color Options](https://github.com/500Foods/WelcomeToTroodon/blob/main/docs/level_2/mmu_options.md) - Print with a mix of colors and materials at the same time
- 🥇 [Toppers](https://github.com/500Foods/WelcomeToTroodon/blob/main/docs/level_2/toppers.md) - Increase the top height or add mounting points for other accessories
- 🙂 [Advanced Calibration](https://github.com/500Foods/WelcomeToTroodon/blob/main/docs/level_2/advanced_calibration.md) - For when you want that extra bit of performance
- 🙂 [Klipper TMC Auto Tune](https://github.com/500Foods/WelcomeToTroodon/blob/main/docs/level_2/klipper_tmc_auto_tune.md) - Let's quiet things down a little

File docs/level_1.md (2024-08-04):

# 🙂 Level One - Welcome!  
This list is aimed at new 3D printer owners, particularly new Troodon 3D printer owners, as well as anyone looking to get more from their existing setup. This is more about the initial few weeks with a new printer and what to have on hand to make that experience as positive and productive as possible. 
No mods here, really, as these are focused on getting up and running with what you already have out of the box with a typical stock configuration.

- 🙂 [Software and Firmware](https://github.com/500Foods/WelcomeToTroodon/blob/main/docs/level_1/software.md) - Get everything up to date
- 🙂 [Tools](https://github.com/500Foods/WelcomeToTroodon/blob/main/docs/level_1/tools.md) - What you need to perform basic assembly, maintenance, and repairs
- 🙂 [Accessories](https://github.com/500Foods/WelcomeToTroodon/blob/main/docs/level_1/accessories.md) - Not strictly required, but a few things to help 
- 🙂 [Chemicals](https://github.com/500Foods/WelcomeToTroodon/blob/main/docs/level_1/chemicals.md) - Keep these on hand for quick cleanup and proper maintenance
- 🙂 [Replacement Parts](https://github.com/500Foods/WelcomeToTroodon/blob/main/docs/level_1/replacment_parts.md) - Stuff is going to break, so be prepared
- 🙂 [Initial Tuning](https://github.com/500Foods/WelcomeToTroodon/blob/main/docs/level_1/initial_tuning.md) - A little extra TLC goes a long way
- 🙂 [First Prints](https://github.com/500Foods/WelcomeToTroodon/blob/main/docs/level_1/first_prints.md) - Good places to start

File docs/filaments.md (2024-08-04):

# 🧐 Fussy Filaments
A critical aspect of 3D printing relates to the type of filament used. While there are many websites that go on at length about the properties of each filament type, at the end of the day it comes down to how well the printer can process the filament being fed to it. There are differences in filament quality between vendors, and sometimes even between colors or batches of the same filament type from the same vendor. There can also be differences related to how dry the filament is. Here is a brief look at the most common filament types and what to plan for in terms of printer capabilities, modifications, settings, and so on.

- [PLA](https://github.com/500Foods/WelcomeToTroodon/blob/main/docs/level_0/pla.md) - Most common, easiest to start with, least expensive
- [PETG](https://github.com/500Foods/WelcomeToTroodon/blob/main/docs/level_0/petg.md) - More durable, less brittle, quite popular
- [TPU](https://github.com/500Foods/WelcomeToTroodon/blob/main/docs/level_0/tpu.md) - Much more flexible and sometimes even stretchy
- [ABS / ASA](https://github.com/500Foods/WelcomeToTroodon/blob/main/docs/level_0/abs.md) - Better for high-temperature environments
- [Nylon](https://github.com/500Foods/WelcomeToTroodon/blob/main/docs/level_0/nylon.md) - Not as strong but very durable, more expensive
- [Additives](https://github.com/500Foods/WelcomeToTroodon/blob/main/docs/level_0/additivies.md) - Glass and Carbon Fiber take things up a notch
- [Others](https://github.com/500Foods/WelcomeToTroodon/blob/main/docs/level_0/others.md) - Many, many more options to choose from

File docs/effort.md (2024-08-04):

# 🤓 Effort, Expertise, and Expense
Almost any kind of upgrade or modification to your printer will require something - a bit of time, a bit of know-how, or a bit of money. Sometimes more than one, and sometimes much more than a bit. To help, a simple rating system has been used throughout these pages. Naturally, everyone values their own time, skills, and money differently. What might be cheap for one person might be out of the question for someone else. The same goes for time and talent - there's a reason why we don't all have Vorons! 

| 🤓 | Effort | Description |
|:-----:|:---:|:---|
| 🙂 | Easy | Items that almost everyone can (and should) implement<ul><li>Not very time-consuming, often much less than an hour</li><li>Not very complex - grandma could do it (supervised, of course)</li><li>Little or no cost - won't impact the filament budget</li></ul> <tr></tr> |
| 🔨 | Medium | Items that are broadly applicable, but strictly optional<ul><li>Might take some time to implement, certainly more than a few minutes </li><li>Definitiely need to read the documentation, maybe even watch a video or two</li><li>Some expense, likely more than the cost of a roll of filament</li></ul> <tr></tr> |
| 🥇 | Difficult | Items that might be very beneficial but complex to implement<ul><li>More of a weekend project than an evening project</li><li>Need to do a bit of planning, watch several videos, do a bit of research</li><li>Likely the cost of several rolls of filament, or more, all-in</li><ul> <tr></tr> |

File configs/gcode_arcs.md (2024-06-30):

# [gcode_arcs]

To enable support for G2/G3 commmands, add the following to printer.cfg
```
[gcode_arcs]
#resolution: 1.0
#   An arc will be split into segments. Each segment's length will
#   equal the resolution in mm set above. Lower values will produce a
#   finer arc, but also more work for your machine. Arcs smaller than
#   the configured value will become straight lines. The default is
#   1mm.
```
NOTE: For Orca, there's a corresponding setting found under `Quality > Precision > Arc fitting`. The help for this option suggests leaving it
turned off as Klipper will convert arcs to segments anyway. 

If you're not using Orca, or if you have G-code files from somewhere else, this should allow Klipper to accept the G2/G3 comamnds.

## Reference
- [Klipper Documentation](https://github.com/Klipper3d/klipper/blob/master/docs/Config_Reference.md#gcode_arcs) - Configuration Reference

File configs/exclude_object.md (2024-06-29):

# [exclude_object]
A relatively recent addition to the Klipper ecosystem was the ability to exclude objects from the currently running print job. 
If your print job contains several objects and one or more of them gets knocked out of place, they can be excluded from that point forward. 
This will stop the printer from trying to print mid-air over a part that is no longer positioned properly, potentially salvaging the rest of the objects in that print job. Very handy!

In order to enable this feature, it is a simple addition of the following to the printer.cfg file.

```
#####################################################################
# Support for canceling objects while printing
#####################################################################
[exclude_object]
```

With that line in place, Mainsail (the web interface for Klipper) will now have a button at the top, where the pause/cancel button is, that will bring up an interface and allow you to exclude objects. 

NOTE: This also requires that your slicer includes labels for the objects and has "exclude objects" enabled as well. In Orca, this can be found under the "Others" tab when the Advanced option is enabled.

## Reference
- [Klipper Documentation](https://www.klipper3d.org/Exclude_Object.html) - Exclude Objects

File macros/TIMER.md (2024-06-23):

# TIMER Macros

An explanation for how to use these can be found [here](https://github.com/500Foods/WelcomeToTroodon/blob/main/docs/level_s/time_timer.md). Note that these macros rely on several supporting [shell scripts](https://github.com/500Foods/WelcomeToTroodon#time-and-timer-shell-scripts).

```
####################################
# TIMER macros
####################################

# These log the current date/time in ISO8601 format

[gcode_shell_command shell_get_current_datetime]
command: ~/scripts/get_current_datetime.sh
timeout: 2.
verbose: True

[gcode_macro current_date_time]
description: Log the current date/time in IOS8601 format
gcode:
    RUN_SHELL_COMMAND CMD=shell_get_current_datetime

# These start a timer by logging a timestamp to a tmp file
    
[gcode_shell_command shell_log_current_datetime]
command: ~/scripts/log_current_datetime.sh
timeout: 2.
verbose: False

[gcode_macro timer_start]
description: Start a named timer
gcode:
    {% set TIMER=params.TIMER | default("Manual_Timer") | string %}
    RUN_SHELL_COMMAND CMD=shell_log_current_datetime PARAMS={TIMER}

# These calculate the eleapsed time by reading in a previous tmp file value

[gcode_shell_command shell_get_elapsed_time]
command: ~/scripts/get_elapsed_time.sh
timeout: 2.
verbose: True

[gcode_macro timer_elapsed]
description: Show the elapsed time of a named timer
gcode:
    {% set TIMER=params.TIMER | default("Manual_Timer") | string %}
    RUN_SHELL_COMMAND CMD=shell_get_elapsed_time PARAMS={TIMER}
```

#
Parent: [Macros Quick Reference](https://github.com/500Foods/WelcomeToTroodon#%EF%B8%8F-macros-quick-reference)

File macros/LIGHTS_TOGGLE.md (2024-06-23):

# LIGHTS_TOGGLE
Many printers, including specifically the Troodon, have a chamber light. This is usually an LED light bar of some kind. It is usually wired up to a pin on the MCU so that it can be programmatically turned on and off. By default, it is turned on when the printer is turned on, and that's
often the end of it. In Mainsail, there's a "chamber light" button you can use to turn the light on or off, but that's about it. So let's expand on that a bit.

In printer.cfg, the pin assigned to the chamber light is assigned. Let's add a macro there to turn it on if it is off, or turn it off if it is on.

```
#####################################################################
# Chamber Lights
#####################################################################
[output_pin case_light]
pin: PE6               // MCU PIN
pwm: false             // Set up pin to work with digital values
shutdown_value: 0      // Turn off when shutting down
value: 1               // Turn on normally

[gcode_macro LIGHTS_TOGGLE]
description: Toggle Chamber Lights
gcode:
    {% if (printer["output_pin case_light"].value)|int == 1 %}
        SET_PIN PIN=case_light VALUE=0
    {% else %}
        SET_PIN PIN=case_light VALUE=1
    {% endif %}
```

We can also take this a step further by adding a light button to KlipperScreen. Changes to KlipperScreen are made in the KlipperScreen.conf file. By default, there's nothing in there other than the "don't change anything below this line" message. 
To add a new menu button to the main page, and then have it call the macro that was just created, add the following section to the very top of KlipperScreen.conf.
```
[menu __main light]
name: Chamber Light
icon: light
method: printer.gcode.script
params: {"script":"LIGHTS_TOGGLE"}
```

After KlipperScreen restarts (and Klipper itself is restarted to enable the macro), there should be a new button on the main screen that can be used to toggle the chamber light.

LIGHTS_TOGGLE (https://github.com/500Foods/WelcomeToTroodon/assets/41052272/e698e328-119f-48d2-8448-b3598d6212f5)

NOTE: Klipper processes macros in a sequential and single-threaded manner. If a long-running macro is currently running, such as a PRINT_START macro, other macros will queue up behind it, and not get executed until it is finished.
Put another way, this means that while something like PRINT_START is running, the light button will appear to not work. But tapping it will queue up the request which will be executed after.

#
Parent: [Macros Quick Reference](https://github.com/500Foods/WelcomeToTroodon#%EF%B8%8F-macros-quick-reference)

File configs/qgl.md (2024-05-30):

# [quad_gantry_level]
Quad Gantry Levelling (QGL) on a Troodon uses the stock Voron TAP mechanism to determine the relative positions of the four corners of the build plate. It then adjusts the motors in each of the four corners to ensure that they are level. 

The gantry can become tilted (not level) in various scenarios, such as when the printer has been off for an extended time, or if the gantry has been bumped or moved manually during maintenace. 
Manually adjusting the gantry should be done to within 1mm if possible in order for this levelling mechanism to work. To help with that, print a set of [gantry levelling supports](https://github.com/500Foods/WelcomeToTroodon/blob/main/docs/level_1/gantry_levelling.md).

Another consideration is to determine the positions on the print bed where the measurements are taken. By default, the configuration uses the extreme edges of the stock build plate. 
If the build plate is not positioned precisely, or if you have a slightly smaller build plate, it is entirely possible that the QGL points will miss the bed entirely. 
In the configuration below, the points are brought in 10mm to compensate for this.

Please make note of the limits and directions of each axis for your printer. For a typical CoreXY printer like a Troodon, this will be as follows.
- X axis runs from 0 at the left to max at the right
- Y axis runs from 0 at the front to max at the back
- Z axis runs from 0 at the bottom to max at the top

A key value is the retry_tolerance, shown below at 0.0075. Ideally this number will be as low as possible, but there are physical limits that come into play. 
If this value is set too low, the QGL process will continually cycle, taking a very long time and ultimately fail. 
If this value is set too high, you won't get all the benefits that are derived from the QGL in the first place - a perfectly level bed.

Ideally, the QGL will test the four points, make an adjustment, and complete. In some cases, it may make 2-3 rounds. If it routinely takes more than that, consider adjusting the retry tolerance. 

If the QGL fails unexpectedly, consider doing a little troubleshooting to see if something else is amiss.
- Out-of-level due to printer being off for an extended period
- Build plate not sufficiently stuck to underlying aluminum base plate
- Build plate not aligned properly with underlying aluminum base plate
- Belt tensioning issues

In most cases, a QGL should be automatically performed before every print. It is included in our [PRINT_START](https://github.com/500Foods/WelcomeToTroodon/blob/main/macros/PRINT_START.md) macro for just this purpose. 
```
#####################################################################
# Quad Gantry Levelling
#####################################################################
[quad_gantry_level]

#--------------------------------------------------------------------
## Example: Gantry Corners for 250mm Build
#--------------------------------------------------------------------
# gantry_corners:
#    -60,-10                # Front-left X/Y
#    310, 320               # Back-right X/Y
# points:
#    50,25                  # Front-left X/Y
#    50,175                 # Back-left X/Y
#    200,175                # Back-right X/Y
#    200,25                 # Front-right X/Y
#--------------------------------------------------------------------
## Example: Gantry Corners for 300mm Build
#--------------------------------------------------------------------
# gantry_corners:
#    -60,-10                # Front-left X/Y
#    360,370                # Back-right X/Y
# points:
#    50,25                  # Front-left X/Y
#    50,225                 # Back-left X/Y
#    250,225                # Back-right X/Y
#    250,25                 # Front-right X/Y
#--------------------------------------------------------------------

# Limts of gantry
gantry_corners:          
   -60,-10                # Front-left X/Y
   410,420                # Back-right X/Y

# Points to measure
points:        
   10,10                  # Front-left X/Y
   10,340                 # Back-left X/Y
   340,340                # Back-right X/Y
   340,10                 # Front-right X/Y

speed: 500                # Horizontal move speed between points
horizontal_move_z: 5      # Vertical movement between points
retry_tolerance: 0.0075   # When everything is very well calibrated
#retry_tolerance: 0.01    # When you want the QGL to complete more quickly
retries: 10               # Number of cycles to run
max_adjust: 10            # How much adjustment is acceptable
```
References:
- [Klipper QGL Documentation](https://www.klipper3d.org/Config_Reference.html?h=probe#quad_gantry_level) - List of parameters

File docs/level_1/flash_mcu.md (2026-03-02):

# Flashing the MCU

A typical 3D printer these days has a bunch of electronics that coordinate all of the printer's components to get the printer to actually print. 
A common configuration uses something called an MCU - basically a small computer, like a Raspberry Pi or even just a CPU or SBC chip, combined with controllers for all the motors, fans, heaters, lights, and so on. In a Troodon 2.0 Pro, as of this writing, that MCU happens to be a custom BigTreeTech Octopus F407-v1. 

Complicating things a little more, Klipper is capable of managing the affairs of multiple such MCUs. It can be, for example, that you have a main MCU running Klipper itself that is an actual Raspberry Pi 4B all on its own. 
Then a separate MCU could be used to control the motors that move the print head around. And maybe another MCU in the printer's toolhead. And a fourth MCU that might be in a Klipper Expander or something like that. All of these then potentially each have their own firmware that will need to be updated from time to time. 
The Troodon 2.0 Pro comes with an accelerometer used for fine-tuning the printer (aka input shaping) that also is, you guessed it, an MCU that has its own firmware.

Instructions for how to update each MCU in your particular printer's configuration will vary, somtimes widely. But they need to be followed very closely to ensure that you're actually updating the right MCU with the right firmware and in such a way as to be careful not to "brick" the MCU. 
In other words, you have to be careful as it is entirely possible to mess it up in such a way that the firmware cannot be updated and the MCU becomes useless and will have to be replaced. Aka, about as useful as a brick. 
And you certainly don't want to apply firmware intended for one MCU onto another - even if they're using the same chips - something that is increasingly problematic as more and more MCUs appear in these kinds of printers.

The good news is that there are instructions for how to do these firmware updates. The bad news is that they're not always all that clear. Let's try and help with that.

## Upgrading the BTT Octopus F407
TBD.

### Reference
- Check your printer.cfg file for instructions specific to your printer
- [Klipper Documentation - SDCard Updates](https://www.klipper3d.org/SDCard_Updates.html)
- [Voron Documentation - Automating Klipper MCU Updates](https://docs.vorondesign.com/community/howto/drachenkatze/automating_klipper_mcu_updates.html)

## Upgrading the firmware
Note: Locate *your* device first.
```
ls /dev/serial-by-id/

sudo service klipper stop
cd ~/klipper/
make clean
make menuconfig
make
make flash FLASH_DEVICE=/dev/serial/by-id/usb-Klipper_stm32f407xx_2D0023000E47323137363638-if00
sudo service klipper start
```

## Updating the ADXL
Here's a start, credit to @dog2bert from the #Troodon Discord community. This has been added as "adxl_update.sh" in the "scripts" folder in this repository. We'll give this a once over a little bit later.

```
#!/usr/bin/bash

sudo service klipper stop
cd ~/klipper
git pull
make clean
make menuconfig
make
make flash FLASH_DEVICE=/dev/serial/by-id/usb-1a86_USB2.0-Serial-if00-port0
sudo service klipper start
```

In Menuconfig:
- Microcontroller: Raspberry Pi RP 2040
- Com Interface: USBSERIAL

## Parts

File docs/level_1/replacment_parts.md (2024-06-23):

# Replacement Parts
- Spare Nozzles / Assorted Nozzle Sizes
- Replacement Build Plates
- Spare PTFE Tubing / Connectors
- Spare Hotends / Heaters / Socks
  
#
Next: [Initial Tuning](https://github.com/500Foods/WelcomeToTroodon/blob/main/docs/level_1/initial_tuning.md)

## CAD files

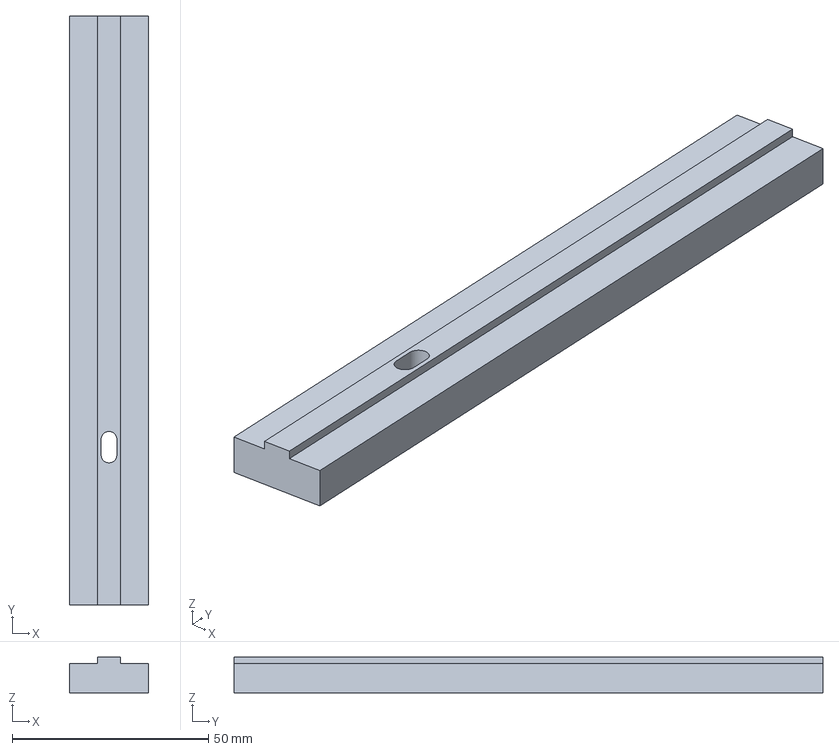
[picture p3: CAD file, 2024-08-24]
3D_Files/RearPanelInserts/Back_Panel_Inserts-SideBottom.3mf
20.0 x 150.0 x 9.10 mm

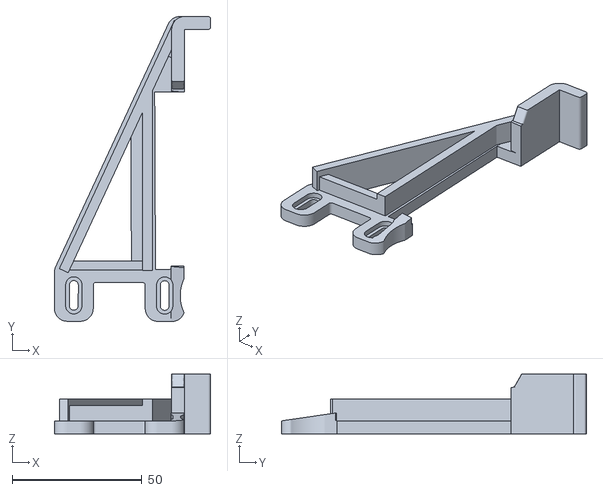
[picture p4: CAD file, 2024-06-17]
3D_Files/Troodon_Alignment_Bracket.stl
60.2 x 117.5 x 23.0

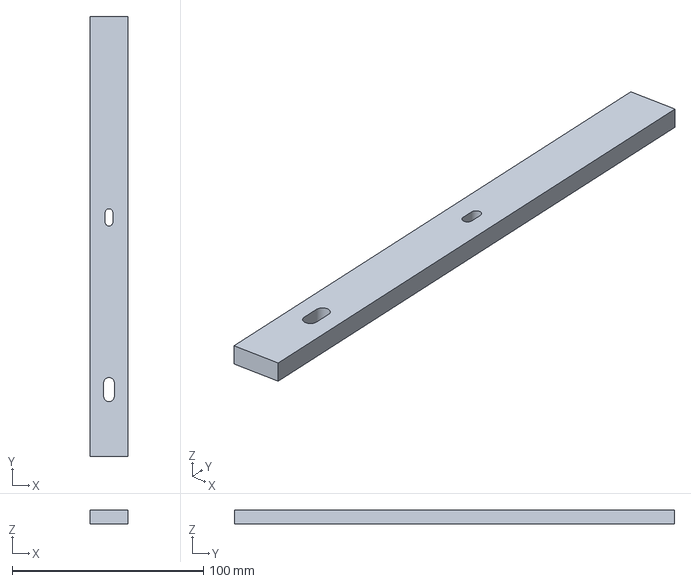
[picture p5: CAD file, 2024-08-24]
3D_Files/RearPanelInserts/Back_Panel_Inserts-TopMiddle.3mf
20.0 x 230.0 x 7.50 mm

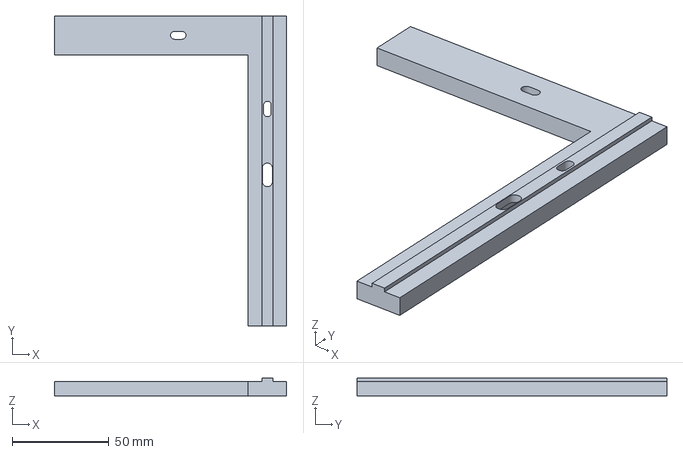
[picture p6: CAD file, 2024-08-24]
3D_Files/RearPanelInserts/Back_Panel_Inserts-TopLeft.3mf
120.0 x 160.0 x 9.10 mm

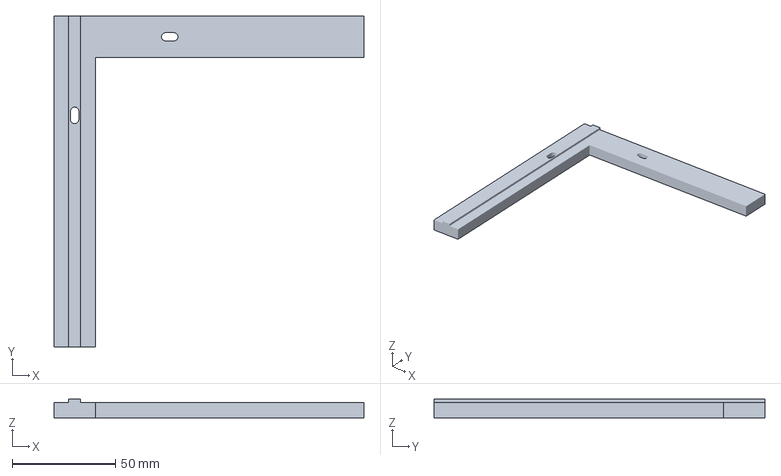
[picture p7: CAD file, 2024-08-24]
3D_Files/RearPanelInserts/Back_Panel_Inserts-TopRight.3mf
150.0 x 160.0 x 9.10 mm

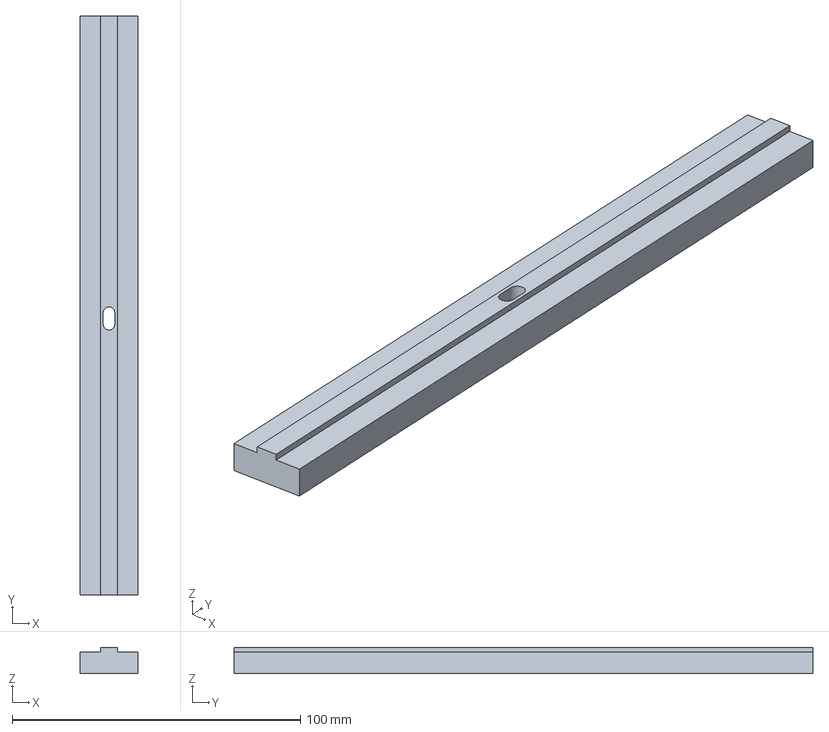
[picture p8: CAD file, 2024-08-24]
3D_Files/RearPanelInserts/Back_Panel_Inserts-SideMiddle.3mf
20.0 x 201.0 x 9.10 mm

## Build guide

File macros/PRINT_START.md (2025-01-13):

# PRINT_START Macro

The PRINT_START macro is typically called at the start of every print job. It is used primarily to configure the printer to a known state in terms of the temperatures of its various components, specifically the extruder (hotend) temperature and the bed temperature. 
It also looks after moving the toolhead to a known position along with various position-related calibration steps.

There are many elements that may be added to such a macro depending on the available hardware, some of which are included in the PRINT_START macro shown below.
- Homing X, Y, and Z 
- Quad-Gantry-Levelling (QGL)
- Nozzle cleaning and priming
- Configure chamber temperatures/heaters
- Initialize custom lighting options
- Initialize custom camera settings
- Log timing or other data

The PRINT_START macro as shown below tries to speed up the process by first setting the temperature targets for the extruder and the bed without waiting for them to reach temperature before continuing. 
This allows for non-heat-related items, like homing the toolhead, to continue while they reach temperature. 
However, it is likely that the slicer will generate the non-wait versions of these very same commands in the generated gcode, even before calling PRINT_START. 
In Orca, for example, these are set in the top-most printer settings under "Machine G-code". Be sure to remove those commands in the generated gcode to take advantage of this optimization.

NOTE: The PRINT_START macro call is added to the gcode sent to the printer by the slicer software. For example, in Orca, it looks like this, which can be found in Print Settings > Machine G-cocde > Machine Start G-code. 
This is where the values for EXTRUDER and BED are derived from in the script.

***NOTE: It is critically important that the call to PRINT_START and its parameters supplied by your [slicer](https://github.com/500Foods/WelcomeToTroodon/tree/main?tab=readme-ov-file#%EF%B8%8F-slicers-quick-reference) 
match the PRINT_START macro in your printer.cfg. Also, review whatever else is being added by your slicer as this may have changed during an update, and may be duplicating some of the work of the PRINT_START macro. 
See the [Orca](https://github.com/500Foods/WelcomeToTroodon/blob/main/configs/orca.md) page for more information on that particular slicer software.***
```
PRINT_START EXTRUDER=[nozzle_temperature_initial_layer] BED=[bed_temperature_initial_layer_single]
```

***NOTE: Sometimes there is also a START_PRINT macro defined in printer.cfg. Unless it is being called by your slicer or by another macro, it can be safely removed.***

As with all the Macros provided here, be sure to examine them thoroughly and comment/uncomment the various parts as needed. Also, note that if there are more console log entries than you'd like to see,
the console log typically has the ability to have filters applied. In Mainsail, you can find these under the Interface Settings (gear icon in the top-right corner), at the bottom of the Console page.

***DISCLAIMER: While every effort is made to ensure that these macros work well in the vast majority of cases, typos or other mistakes made in these macros can lead to bad things happening. 
Please be sure to thoroughly test any changes you make to your own printer configuration, and also be sure to factor in any modifications you have made from your stock configuration.***

```
####################################
# PRINT_START macro
####################################
[gcode_macro PRINT_START]
description: Prepare the printer for a new print job
gcode:

    # Log the start of the script
    M118 PRINT_START has started

    # Start a timer (Note: Requires TIMER macros)
    # RUN_SHELL_COMMAND CMD=shell_get_current_datetime
    # RUN_SHELL_COMMAND CMD=shell_log_current_datetime PARAMS='PRINT_START'
    # RUN_SHELL_COMMAND CMD=shell_log_current_datetime PARAMS='__COMPLETED'
    # RUN_SHELL_COMMAND CMD=shell_log_current_datetime PARAMS='__CANCELLED'

    # Get the extruder temperature expected for this print job
    # This will typically be a value in the range 220-260C
    {% set temp_extruder  = params.EXTRUDER|default(260)|int %}

    # Set extruder temperature (without waiting) initially
    M104 S{temp_extruder}       # No Waiting
    # M109 S{temp_extruder}     # Waiting

    # Get the bed temperature expected for this print job
    # This will typically be a value in the range 50-110C 
    {% set temp_bed  = params.BED|default(100)|int %}

    # Set the bed temperature (without waiting) initially
    M140 S{temp_bed}            # No Waiting
    # M190 S{temp_bed}          # Waiting

    # Home the printer (X, Y, and Z)
    G28

    # Reset the length of filament extruded to zero
    G92 E0      

    # Now we wait for the extruder temp to do a NOZZLE_CLEAN
    # then turn on the part fan so it gets back down to 150C
    # for the next step
    M109 S{temp_extruder}       # Wait for extruder to get to temp
    NOZZLE_CLEAN                # Clean nozzle
    M106                        # Set part cooling fan to max
    M104 S150                   # Set extruder temp to 150C (no waiting)
      
    # This starts the Quad-Gantry-Levelling process, aka QGL
    # Several additional steps may be performed here as well
    # Be sure to check the G32 Macro for specifics, but this
    # will typically include setting the temp to 150C and
    # running NOZZLE_CLEAN in addition to the QGL.
    G32       

    # Turn off part cooling fan we turned on earlier
    M106 S0

    # One of these is used to either load a previously generated
    # bed mesh, or create a new bed mesh each time.
    # If you change build plates constantly, or if you have a
    # Beacon or similar probe that is very quick, performing
    # a bed mesh for each print is a pretty good idea.
    # Otherwise, it can take a lot of time per print.
    # NOTE: Bed mesh data is stored at the end of printer.cfg
    # BED_MESH_CALIBRATE PROFILE=mesh1 METHOD=automatic
    BED_MESH_PROFILE LOAD=mesh1

    # Change printer to absolute positioning mode
    G90

    # Move to middle of the print bed (assuming a 350mm x 350mm bed)
    G1 X175 Y175

    # Wait for extruder to get to print temp
    M109 S{temp_extruder}

    # Wait for bed to get to print temp
    M190 S{temp_bed}

    # One last clean 
    NOZZLE_CLEAN

    # Try a print
    # NOZZLE_PRIME

    # One last home
    G28

    # Show elapsed time (Note: Requires TIMER macros)
    # RUN_SHELL_COMMAND CMD=shell_get_elapsed_time PARAMS='PRINT_START'

    # Log the end of the script
    M118 PRINT_START has ended
```
## Why 150C?
Finally, a note about 150C. The QGL and potentially the bed leveling that occurs is generally performed at 150C. So in essence, we have a situation where the following occurs.
- Increase nozzle temperature to printing value, say 260C (depends on filament)
- Nozzle clean
- Reduce nozzle temperature to 150C
- QGL
- Increase nozzle temperature to back to printing value
- Nozzle Clean
- Print

If you have a fast nozzle heater, like a ceramic heater, this happens very quickly. If you don't, this can take an agonizingly long time. But why do this at all?

Well, the nozzle is ideally set at printing temperature to ensure it can be properly cleaned. Any filament stuck to the tip of the nozzle might not come off otherwise. In practice, filament tends to be not stuck to the nozzle but rather simply extruded and thus dangling, and it would get removed when doing a nozzle clean at any temperature.

The QGL and, optionally, the bed levelling, is done at 150C. One reason given is that this is to prevent damage to the build plate or even the underlying base plate. Constant TAP contact at high temperatures at identical points will lead to damage, and a lower temperature will reduce that possibility. It may also be that build plates have improved, and TAP itself has improved, likely to the point where this isn't an issue. Another reason given is to have a low enough temperature to ensure that a TAP doesn't lead to filament coming out of the nozzle. As the nozzle is the primary sensor in play with TAP, having material extruded while TAPing would be a serious problem.  150C is below the temperature at which this occurs for PLA. So if you never use PLA, then this value can be set significantly higher, thus reducing the time to get to/from the printing temperature.

NOTE: The 150C QGL temperature is set explicitly in the PRINT_START script above, but it is likely also set when running a QGL, which can be found in the G32 macro in printer.cfg.

## Troubleshooting
Here are a few additional notes to help with troubleshooting the PRINT_START macro. These are intended specifically for new users of the Troodon 2.0 Pro which ships with a macro that doesn't quite work properly with current versions of Orca.

1. Double-check that the [Orca settings](https://github.com/500Foods/WelcomeToTroodon/blob/main/configs/orca.md) for calling PRINT_START with the EXTRUDER and BED parameters match the same parameters in the PRINT_START macro.
1. Double-check that the [Orca settings](https://github.com/500Foods/WelcomeToTroodon/blob/main/configs/orca.md) don't also include temperature commands as all the necessary commands for the bed and extruder are included in PRINT_START already. Remove any extraneous M109 commands, for example.
1. The PRINT_START macro was recently updated with extra "PRINT_START has started" and "PRINT_START has ended" messages output to the console so you can confirm that it is in fact this version of the macro that is running.
1. This was also to address the problem of people editing printer.cfg and not saving the changes, or not rebooting after, or updating a different printer.cfg file.
1. Any and all changes to printer.cfg require rebooting Klipper to have the changes take effect. If you edit the printer.cfg file while Klipper is currently printing, it will allow you to save the file, but you will still have to restart Klipper after the print completes for the updated printer.cfg changes to take effect.
1. There are often several printer.cfg files with timestamps. These are generated whenever you do a new bed mesh levelling, so be careful not to make changes to those as only the base "printer.cfg" file is actually used by Klipper.
1. The PRINT_START macro can be run directly from the web interface without using Orca at all. It will do the same steps - heating to print temperature, then to 150C to do a QGL, and then back to print temperature. Running the macro in this way may help track down issues with the macro itself. Note that by default, the NOZZLE_PRIME command is commented out, so the PRINT_START macro does not actually attempt to extrude anything and as such should never give an extruder temperature error.
1. When running the PRINT_START macro from the web interface, it will end with the extruder at 260C and the bed at 100C as per the defaults in the PRINT_START macro.
1. You can change those defaults by editing the printer.cfg file and editing the macro itself.
1. When running the PRINT_START macro from the web interface, you can also enter the EXTRUDER and BED values directly by clicking on the arrow on the right side of the macro button.
1. As part of the PRINT_START sequence of commands, it loads a pre-existing "mesh1" bed mesh. If you've not yet done a bed mesh leveling, use the "mesh leveling" and "save mesh" macros to generate one. The "mesh1" name is used by default.
1. Check that there is only one PRINT_START macro defined in printer.cfg. Comment out or remove any others.
1. Check that there is no START_PRINT macro defined in printer.cfg. Comment out or delete any that are present.

#
Parent: [Macros Quick Reference](https://github.com/500Foods/WelcomeToTroodon#%EF%B8%8F-macros-quick-reference)

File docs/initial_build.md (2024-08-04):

# ⚠️ Initial Build Tips
Before putting together your 3D printer there are a few things to be aware of. These items are targeted at those assembling a Troodon printer but may be of interest to others. These items might have been overlooked (or not included) in the assembly guide. 
- [Linear Rails](https://github.com/500Foods/WelcomeToTroodon/blob/main/docs/level_0/linear_rails.md) - Smooth operation is not optional
- [Base Plate Screws](https://github.com/500Foods/WelcomeToTroodon/blob/main/docs/level_0/bed_plate.md) - How tight is too tight?
- [Belt Tensioning](https://github.com/500Foods/WelcomeToTroodon/blob/main/docs/level_0/belt_tensioning.md) - Also, how tight is too tight?
- [T-Nuts](https://github.com/500Foods/WelcomeToTroodon/blob/main/docs/level_0/tnuts.md) - Friend or foe?
- [Acrylic Panels](https://github.com/500Foods/WelcomeToTroodon/blob/main/docs/level_0/acrylic_panels.md) - Enclosures are great, right?
- [First Problems](https://github.com/500Foods/WelcomeToTroodon/blob/main/docs/level_0/first_problems.md) - Forewarned is forearmed!

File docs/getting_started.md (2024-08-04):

# 🤔 Getting Started Resources
Even before your printer is up and running, there are plenty of resources to check out. Both to learn more about 3D printing in general, if you are new to this space, and for considerably more in-depth knowledge about getting the most out of your printer.
- [Documentation](https://github.com/500Foods/WelcomeToTroodon/blob/main/docs/level_0/documentation.md) - User manuals, online guides, and other reference materials
- [Discord Communities](https://github.com/500Foods/WelcomeToTroodon/blob/main/docs/level_0/discord.md) - Connect with users and vendors of popular prints and products
- [Vendor Websites](https://github.com/500Foods/WelcomeToTroodon/blob/main/docs/level_0/vendors.md) - Vetted suppliers with a history of delivering on their promises
- [YouTube Videos](https://github.com/500Foods/WelcomeToTroodon/blob/main/docs/level_0/youtubers.md) - Helpful accounts to follow, covering a wide range of topics
- [Troodon Information](https://github.com/500Foods/WelcomeToTroodon/blob/main/docs/level_0/troodon.md) - Links to check out if you're on the fence about purchasing a Troodon
- [Notes About Mods](https://github.com/500Foods/WelcomeToTroodon/blob/main/docs/level_0/modifications.md) - What is a mod and why are they so popular?

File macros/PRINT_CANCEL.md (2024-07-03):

# PRINT_CANCEL
A print generally ends in one of two ways - either it is successful and completes normally, or something goes awry and you cancel it. Klipper can be configured to do different things in each case.
Here, we're addressing what to do when a print is prematurely canceled. Note that if an "emergency stop" mechanism is used, this macro will not be executed.

The main things we're doing here are calling the timer to log the elapsed time if the TIMER macros are being used, and then positioning the toolhead out of the way. In this example, it is moved
to the front of the printer, center-top, so it is easy to have a look at the nozzle and see if anything is amiss. This can also serve as a visual cue that the print was canceled. 
Note that a print could be canceled automatically due to missed temperature targets and that kind of thing.

NOTE: For this to be called, Klipper must be told about it. This is handled using the "on_error_gcode" directive which typically appears near the top of the printer.cfg file. 
It, and the PRINT_CANCEL macro, may already exist or might not be present. Be sure to also check for CANCEL_PRINT macro and consider combining the two into one macro. 
Alternatively, this directive could be added to the g-code generated by the slicer.
``` 
on_error_gcode: PRINT_CANCEL
```
NOTE: Due to the single-threaded nature of Klipper and other aspects of its core architecture, running the PRINT_CANCEL macro doesn't usually immediately stop the print. It will complete the G-code 
command it is currently working on. If that's printing a line of filament, as in a NOZZLE_PRIME, then the entire line will print before it recognizes the cancel request. If it is running another
macro, that macro will complete before the request for PRINT_CANCEL is dealt with.

In particular, if the PRINT_START macro is running, Klipper will wait until the *entire* macro completes before acknowledging the cancel request. 
It may often be quicker to use the emergency stop function and restart Klipper rather than wait for it to finish, particularly if you want to cancel a print job before it has laid down any filament. 
```
######################################
# PRINT_CANCEL macro
#######################################
[gcode_macro PRINT_CANCEL]
description: Cancel print abruptly
gcode:

    # Show elapsed time (Note: Requires TIMER macros)
    # RUN_SHELL_COMMAND CMD=shell_get_elapsed_time PARAMS='__CANCELLED'
    
    # Retract filament if possible
    {% if printer.extruder.can_extrude %}
        G91               # Relative positioning
        G1 E-5.00 F1000   # Retract 5mm of filament
    {% else %}
        M118 PRINT_CANCEL: Extruder Temp: {printer.extruder.temperature}
        M118 PRINT_CANCEL: Extruder too cool to retract
    {% endif %}

    # The toolhead is presented for inspection following a failure
    {% if printer.toolhead.homed_axes == "xyz" %}
        {% set x_park = (printer.configfile.settings['stepper_x'].position_max - printer.configfile.settings['stepper_x'].position_min) / 2 %}
        {% set y_park = printer.configfile.settings['stepper_y'].position_min %}
        {% set z_park = printer.configfile.settings['stepper_z'].position_max %}

        {% set x_speed = printer.configfile.settings['stepper_x'].homing_speed * 60.0 %}  # homing = mm/s, but F = mm/min 
        {% set y_speed = printer.configfile.settings['stepper_y'].homing_speed * 60.0 %}  # homing = mm/s, but F = mm/min 
        {% set z_speed = printer.configfile.settings['stepper_z'].homing_speed * 60.0 %}  # homing = mm/s, but F = mm/min

        G90                          # Absolute positioning
        G1 Z{z_park} F{z_speed}      # Max Z first
        G1 X{x_park} F{x_speed}      # Center X
        G1 Y{y_park} F{y_speed}      # Front Y
    {% else %}
        M118 PRINT_CANCEL: No movement as printer is not homed
    {% endif %}

    # Turn off heaters - let things cool down
    TURN_OFF_HEATERS                       

    # Turn on part cooling fan to max to cool nozzle
    M106

    # Exhaust fan to max (Note: Requires [fan_generic exhaust_fan] configured)
    # SET_FAN_SPEED FAN=exhaust_fan SPEED=1.0  # Exhaust fan to max -> cool chamber fast

    # Unpause if paused
    CLEAR_PAUSE

    # Cancel the job
    BASE_CANCEL_PRINT

#######################################
# CANCEL_PRINT macro
#######################################
[gcode_macro CANCEL_PRINT]
rename_existing: BASE_CANCEL_PRINT
gcode:
    PRINT_CANCEL
    BASE_CANCEL_PRINT
```

#
Parent: [Macros Quick Reference](https://github.com/500Foods/WelcomeToTroodon#%EF%B8%8F-macros-quick-reference)

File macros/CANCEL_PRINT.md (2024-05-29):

# CANCEL_PRINT
A print generally ends in one of two ways - either it is successful and completes normally, or something goes awry and you cancel it. Klipper can be configured to do different things in each case.
Here, we're addressing what to do when a print is prematurely cancelled. Note that if an "emergency stop" mechanism is used, this macro will not be executed.

The main things we're doing here are calling the timer to log the elapsed time, if the TIMER macros are being used, and then positioning the toolhead out of the way. In this example, it is moved
to the front of the printer, center-top, so it is easy to have a look at the nozzle and see if anything is amiss. This can also as a visual cue that the print was cancelled. 
Note that a print could be cancelled automatically due to missed temperature targets and that kind of thing.

```
#######################################
# CANCEL_PRINT
#######################################

[gcode_macro CANCEL_PRINT]
description: Cancel print abruptly
rename_existing: BASE_CANCEL_PRINT
gcode:

    # Show elapsed time (Note: Requires TIMER macros)
    # RUN_SHELL_COMMAND CMD=shell_log_current_datetime PARAMS='__CANCELLED'
   
    # Retract filament
    G91                   # Relative positioning
    G1 E-5.00 F1000       # Retract 5mm of filament

    # Pick a final position - Assuming a 350mm x 350mm x 310mm print volume
    # Here, the toolhead is presented for inspection following a failure
    G90                   # Absolute positioning
    G1 Z310               # Max Z first
    G1 X175               # Center X
    G1 Y10                # Front Y
    
    CLEAR_PAUSE
    BASE_CANCEL_PRINT
```

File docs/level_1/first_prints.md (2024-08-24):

# First Prints
- [Benchy](https://www.3dbenchy.com/) - Easily the most popular calibration print 
- [Califlower Calibration Tool](https://vector3d.shop/products/califlower-calibration) - Used to calibrate printer dimensional accuracy and skew
- [StealthBurner Latch](https://github.com/500Foods/WelcomeToTroodon/blob/main/docs/level_1/first_print_latch.md) - A better version of a frequently broken part
- [StealtBurner Toolhead ](https://github.com/VoronDesign/Voron-Stealthburner/tree/main/STLs)- Just in case anything else breaks
- [Gantry Levelling "Beer Cans"](https://www.printables.com/model/869496-gantry-leveling-beer-cans-voron-gantry-leveling-ai) - Used to manually level the gantry

## For the Troodon 2.0 Pro 
- [Troodon Filament Runout Sensor Mount](https://www.printables.com/model/568188-filament-sensor-bracket-for-troodon-20) - Don't just leave it hanging
- [Troodon Z-Belt Covers](https://www.printables.com/model/926813-troodon-20-z-belt-covers) - Keep debris from falling into the belts
- [Troodon Motor Mount Covers](https://www.printables.com/model/900588-troodon-20-motor-mount-covers) - Add a little bling to your printer
- [Troodon Bed Alignment Guides](https://github.com/500Foods/WelcomeToTroodon/blob/main/docs/level_1/bed_alignment.md) - These help ensure the build plate is positioned accurately
- [Troodon Corner Brackets](https://github.com/TeamGloomy/Troodon-V2/blob/improved/STL_Files/Formbot/Corner_Piece/Troodonv2cornerpieces.STL) - When you want to change up the color scheme
- [Troodon Rocker Feet](https://www.printables.com/model/629765-troodon-20-rocker-feet) - Makes getting into the electronics bay a little easier
- [Troodon Back Panel Spacers](https://github.com/500Foods/WelcomeToTroodon/blob/main/docs/level_0/acrylic_panels.md) - Give a little more room between the gantry and the back panel
- [Troodon Front Door Magnets](https://www.printables.com/model/916927-troodon-20-pro-front-door-magnets) - "Get rid of those rattly, ugly kitchen cabinet magnets and make your front panels feel loved"
#
Next: [Level Two](https://github.com/500Foods/WelcomeToTroodon#-level-two---get-to-work)

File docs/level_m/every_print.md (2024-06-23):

# Between Every Print

- [ ] 🙂 &nbsp; 01 &nbsp; - &nbsp; Check that the nozzle is clean and give it a good brush
- [ ] 🙂 &nbsp; 02 &nbsp; - &nbsp; Check filament path for dust or other irregularities
- [ ] 🙂 &nbsp; 03 &nbsp; - &nbsp; Check the build plate surface and clean or apply adhesive as required
- [ ] 🙂 &nbsp; 04 &nbsp; - &nbsp; Check the build plate position if using a removable build plate
- [ ] 🙂 &nbsp; 05 &nbsp; - &nbsp; Review timelapse from prior print for issues
- [ ] 🙂 &nbsp; 06 &nbsp; - &nbsp; Check for any parts from the previous print left behind
- [ ] 🙂 &nbsp; 07 &nbsp; - &nbsp; Check whether there is enough filament for the next print

When changing the filament (when not using an MMU): 

- [ ] 🙂 &nbsp; 08 &nbsp; - &nbsp; Position the print head somewhere convenient and ensure the nozzle is clean
- [ ] 🙂 &nbsp; 09 &nbsp; - &nbsp; Check that the nozzle temp is appropriate for the filament being unloaded
- [ ] 🙂 &nbsp; 10 &nbsp; - &nbsp; Use the "Unload Filament" macro to retract the filament
- [ ] 🙂 &nbsp; 11 &nbsp; - &nbsp; Pull the filament out (usually from the back of the printer, not the print head)
- [ ] 🙂 &nbsp; 12 &nbsp; - &nbsp; Cut the end of the filament to square off the end, or sharpen it, in preparation for its next use
- [ ] 🙂 &nbsp; 13 &nbsp; - &nbsp; Use the [NoClogger](https://www.etsy.com/ca/listing/1203822782/noclogger-the-must-have-3d-printing-tool) tool, if you've got one, to clean out the filament path
- [ ] 🙂 &nbsp; 14 &nbsp; - &nbsp; For the new filament, cut the end, or sharpen it, if it isn't already prepared for use
- [ ] 🙂 &nbsp; 15 &nbsp; - &nbsp; If printing from a filament dry box, check the settings of the dry box
- [ ] 🙂 &nbsp; 16 &nbsp; - &nbsp; Check that the nozzle temp is appropriate for the filament being loaded
- [ ] 🙂 &nbsp; 17 &nbsp; - &nbsp; Feed the filament until it reaches the print head
- [ ] 🙂 &nbsp; 18 &nbsp; - &nbsp; Use the "Load Filament" macro and check that the new filament is extruded
- [ ] 🙂 &nbsp; 19 &nbsp; - &nbsp; Clean out the extruded filament and give the nozzle a good brush
- [ ] 🙂 &nbsp; 20 &nbsp; - &nbsp; Use the "Nozzle Clean" and "Nozzle Purge" macros to ensure everything is ready

#
Next: [Weekly Maintenance](https://github.com/500Foods/WelcomeToTroodon/blob/main/docs/level_m/weekly.md)

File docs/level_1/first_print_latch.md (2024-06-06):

# StealthBurner Latch
For Troodon printers, or any printer using the Voron StealthBurner toolhead. There is a latch that is part of the design of the ClockWork 2 extruder that it uses.
When unlocked, it opens up the filament path, allowing for the filament to proceed unobstructed through the extruder directly into the hotend. This can be helpful when changing filaments or troubleshooting problems. 
Generally, FILAMENT_LOAD and FILAMENT_UNLOAD macros should be used instead, removing the need to use the latch entirely.

The issue, however, is that the latch itself isn't particularly strong and is prone to breaking. And, once broken, the extruder is effectively disabled as there's nothing to force the gears that push the filament into the correct position. 
And if you happen to have only one printer, printing a replacement latch is going to be problematic. Fortunately, a little crazy glue can help put a broken latch back together in most cases. But maybe it would be 
best to print up a couple in advance, and while we're at it, print a beefier version that is much less likely to be broken in the first place. Be sure to print these with ABS or ASA or something stronger.



Resources:
- Printables - https://www.printables.com/model/508340-updated-latch-for-voron-stealthburner-clockwork-2-

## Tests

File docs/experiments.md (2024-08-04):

# 💣 Experimental Projects
And something for the brave souls who made it this far. Here you'll find stuff that isn't ready for primetime but may still be useful. The usual disclaimers apply - enter at your own risk, here be dragons, not for the squeamish, etc., etc. 
- [2D Print Transfers](https://github.com/500Foods/WelcomeToTroodon/blob/main/docs/level_e/transfers.md) - Add full-color 2D images to the first layer of your 3D prints.
- [Recycling Printer Waste](https://github.com/500Foods/WelcomeToTroodon/blob/main/docs/level_e/recycling.md) - From support material to failed prints to calibrations, what to do about waste
- [Philement/carbon](https://github.com/500Foods/Philement/blob/main/elements/006-carbon/README.md) - On-device print failure monitoring using Timelapse images

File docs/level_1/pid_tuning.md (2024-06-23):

# 🙂 PID Tuning
A critical component in any 3D printer is the hotend. In particular, the heater at the bottom of the toolhead, just above the nozzle, is where the filament is melted just prior to being pushed out through the nozzle. 
Maintaining a constant temperature here is important to ensure a smooth and consist flow of filament. 

The way the heater works is rather simple. Power is applied to a heating element, perhaps a 24V core that is bolted inside of an aluminum block. Or maybe its a ceramic heater. 
Regardless, when power is applied or increased, the heater gets hotter. When power is removed or decreased, the heater gets cooler. The ***rate*** at which the heater changes temperature is the important part. 
And each part of the heater contributes to how this rate changes. Ceramic heaters can heat up surprisingly fast, for example, whereas a large aluminum block might take some time to reach the same temperature.

To deal with these kinds of variants, Klipper uses something called PID Tuning, where PID stands for "proportional-integral-derivative". Sounds a lot like calculus because, well, it is. The idea is to have the
printer itself run through a series of heating and cooling cycles to determine the relationship between the power being applied (or removed) and the resulting temperature. The end result is a few cryptic values
that get stored in printer.cfg that describe that precise relationship. This helps ensure that the printer can maintain a constant temperature throughout the entire print job.

## When to run a PID Tune?
Extruder PID Tuning should be performed anytime there is a significant change in the toolhead. A different heater, obviously, but also if you're using a different kind of nozzle or a different thermistor, etc. 
Basically, anything that would have an impact on that power-temperature relationship. 

The clue that a PID Tune is necessary is when the temperature graph for either the extruder or the bed is no longer smooth. If the temperature oscillates when it is suppose to be stable, or if it overshoots the
target temperature when heating (or cooling), then this is a good sign that a PID Tune would be helpful.

## PID Tuning - Extruder
Lots of words, but how do we actually kick off a PID Tuning session? Pretty easy, as it turns out.

- Start when the printer and print bed are at room temperature
- Home the printer as you normally would, with the toolhead in the middle of the build plate
- Raise the Z axis off the bed around 50mm so the bed temperature isn't affecting the extruder
- Determine the TARGET temperature for the PID Tune - the temperature you most often print at
- Run the following command in the Klipper console, setting TARGET to that temperature 
```
PID_CALIBRATE HEATER=extruder TARGET=260
```
The printer will then heat up the extruder to that temperature and then oscillate a handful of times. This might take a few minutes,
depending on what kind of heating element is available. 
When complete, it will output a message indicating the optimal values it has determined from its calibration run. To save these
values in printer.cfg, run the SAVE_CONFIG command as indicated. Klipper will then immediately restart and use these values.

## PID Tuning - Bed Heater
The bed heater works the same way, just usually a little slower than the extruder heater. PID Tuning can be done here using the same approach. Use whatever bed temperature here that you normally use for printing.
ABS/ASA prints are typically run with a 100C bed, for example.
```
PID_CALIBRATE HEATER=heater_bed TARGET=100
```
Changing the bed heater or anything related to the components involved in maintaining a consistent bed temperature would be a good time to run this calibration.

#
Next: [First Prints](https://github.com/500Foods/WelcomeToTroodon/blob/main/docs/level_1/first_prints.md)

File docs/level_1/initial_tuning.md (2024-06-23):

# Initial Tuning
While most printers, including Troodons, come already preconfigured whenever possible, there are usually a few things to keep an eye on. And if you ever make changes to anything, particularly with respect to the toolhead, then it is very likely that some calibration is in order.

- 🔨 [Lubricate Rails](https://github.com/500Foods/WelcomeToTroodon/blob/main/docs/level_1/lubrication.md) - Some printers don't ship with lubricated rails
- 🙂 X/Y/Z Limits - How far the toolhead can move in each direction
- 🙂 Belt Tensioning - Not too loose, not too tight, but just right
- 🙂 [PID Tuning](https://github.com/500Foods/WelcomeToTroodon/blob/main/docs/level_1/pid_tuning.md) - Calibrate your heating elements for optimal performance

#
Next: [First Prints](https://github.com/500Foods/WelcomeToTroodon/blob/main/docs/level_1/first_prints.md)

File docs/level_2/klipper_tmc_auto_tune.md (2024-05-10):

# Klipper TMC Auto Tune

### Reference
- [Klipper TMC Auto Tune](https://github.com/andrewmcgr/klipper_tmc_autotune)

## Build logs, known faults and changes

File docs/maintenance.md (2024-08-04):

# ⏰ Routine Maintenance
As complex as they are, 3D printers do require some amount of ongoing routine maintenance. Both in terms of software/firmware, as well as hardware - physical maintenance. How much maintenance depends largely on how much printing is going on. But even printers sitting idle will need maintenance - perhaps even more than if they are used regularly. 

- [Notifications](https://github.com/500Foods/WelcomeToTroodon/blob/main/docs/level_m/notifications.md) - Items that need your immediate attention
- [Between Every Print](https://github.com/500Foods/WelcomeToTroodon/blob/main/docs/level_m/every_print.md) - Good habits will save a lot of trouble down the road
- [Weekly Maintenance (Every 100 Print Hours)](https://github.com/500Foods/WelcomeToTroodon/blob/main/docs/level_m/weekly.md) - Or every 100 print hours
- [Monthly Maintenance (Every 500 Print Hours)](https://github.com/500Foods/WelcomeToTroodon/blob/main/docs/level_m/monthly.md) - Or every 500 print hours
- [Seasonal Maintenace (Every 2,000 Print Hours)](https://github.com/500Foods/WelcomeToTroodon/blob/main/docs/level_m/seasonal.md) - Or every 2,000 print hours

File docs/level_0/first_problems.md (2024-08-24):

# First Problems
- [PRINT_START](https://github.com/500Foods/WelcomeToTroodon/blob/main/macros/PRINT_START.md) Issue - "Extruder not hot enough" and other problems that come as a result of a problematic PRINT_START macro
- X-EndStop Issue - The X-Endstop on the toolhead might not be getting tripped when expected
- Bed Placement - Moving the bed forward or backward if it isn't positioned properly
- Hitting the Doors - Adjust the limits in printer.cfg to prevent this from happening
- Crazy Bed Meshes - Tacos? Did someone say Tacos?
- ["Unable to load panel network"](https://github.com/500Foods/WelcomeToTroodon/blob/main/docs/level_0/network_panel.md) - When you try to configure your WiFi connection
- [Moonraker Warnings](https://github.com/500Foods/WelcomeToTroodon/blob/main/docs/level_1/moonraker_warnings.md) - Crowsnest and Timelapse issues after updating Klipper

#
Next: [Level One](https://github.com/500Foods/WelcomeToTroodon#-level-one---welcome)

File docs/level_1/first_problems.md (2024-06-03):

# First Problems
- PRINT_START Issue - "Extruder not hot enough" and other problems that come as a result of a problematic PRINT_START macro
- X-EndStop Issue
- Bed Placement 
- Hitting the Doors
- Crazy Bed Meshes
- [Moonraker Warnings](https://github.com/500Foods/WelcomeToTroodon/blob/main/docs/level_1/moonraker_warnings.md) - Crowsnest and Timelapse issues after updating Klipper

Next: [Level Two: TAP Upgrades](https://github.com/500Foods/WelcomeToTroodon/blob/main/docs/level_2/tap_upgrades.md)

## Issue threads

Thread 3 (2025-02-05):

BTT Smart Filament sensor v2.0 - guide

CriticalPaint, 2025-02-05:
Ok so my initial plan was to configure and set a delay of 'X' seconds after the purge line to ensure the print would start and not pause because of the filament not moving from the purge line to where the print starts, I couldn't get this working mainly because the macro was giving me no end of grief. So, I was shown by someone in the Klipper discord to just disable and enable the switch via start up code.

Originally, I was trying to use the exp1 slot on the stock Troodon board but could not define the pin properly for the macros to work, which led me to using the 'spare' ports on the LDO Nite Hawk

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

I configured this be as follows.

GPIO3 = Green
GPIO2 = Blue
GND = Black
3V3 = Red

And fed the cables down the x-chain, the y-chain, the z-chain and fed the wires thought the base of the machine and out the back grill and then up the cable management tube.

FIRST PROBLEM:
The stealth burner is a snug unit, and where the ports on the Nitehawk sit you need to make some room, I only realised AFTER I soldered the pins so I can plug the cables in, so if you can, get a low profile set of pins and connectors, or you will have to cut a section out of the stealth burner to accommodate, if I wasn't upgrading I would have been a bit gentler, but my disdain for the stealth burner prompted my decision to get medieval on its arse.

So, once the cables and everything was all installed, we get to the code.

I have this as the module for defining and enabling the BTT SFSv2 in my printer.cfg

#####################################################################
#   Filament Runout Sensor
#####################################################################
[filament_switch_sensor switch_sensor]
switch_pin: nhk:gpio2
pause_on_runout: False
runout_gcode:
 PAUSE # [pause_resume] is required in printer.cfg
 M117 Filament switch runout
insert_gcode:
 M117 Filament switch inserted

[filament_motion_sensor encoder_sensor]
switch_pin: nhk:gpio3
detection_length: 3.5 # accuracy of motion sensor 2.88mm
extruder: extruder
pause_on_runout: False
runout_gcode:
 PAUSE # [pause_resume] is required in printer.cfg
 M117 Filament encoder runout
insert_gcode:
 M117 Filament encoder inserted

The important bit is the macros for this to do its thing.

Here is the print start
#####################################################################
# Macro-Print_Start
#####################################################################
#   Use PRINT_START for the slicer starting script - please customise for your slicer of choice
[gcode_macro PRINT_START]
gcode:
   # disable the sensor
    SET_FILAMENT_SENSOR SENSOR=encoder_sensor ENABLE=0
    # rest of the magic
    G32                            ; home all axes
    G90                            ; absolute positioning
    G1 Z20 F3000                   ; move nozzle away from bed
    NOZZLE_PRIME
    #Enable Filament Sensor
    SET_FILAMENT_SENSOR SENSOR=encoder_sensor ENABLE=1

#   Use PRINT_END for the slicer ending script - please customise for your slicer of choice

You do not really need anything for the print end as the commands are simply turning on and turning off the switch in question,

How this works is
1.	A job is set to print,
2.	The sensor is switched off,
3.	The printer homes,
4.	The printer goes through the heat up routine,
5.	The printer goes through the quad gantry level.
6.	The printer primes the nozzle.
7.	The sensor is switched on,
8.	The print moves to position and starts printing.

Note: I have set my detection length to 3.5mm instead of the 2.88mm as the default, this is long enough ( for my scenario) to not trigger the pause function all the time, it depends on speed, flow rate, squish etc, this will require the most testing for your environment, I did this by printing a  '9 square bed level test' its small and doesn't use a lot of filament and its done in 10 minutes

This setup will pause on filament runout and when the filament stops moving for any reason, which is exactly what I wanted. I hope this helps those who were in the same boat as me.

500Foods, 2025-02-05:
Great, I'll add this to the HOWTO section:

https://github.com/500Foods/WelcomeToTroodon/blob/main/docs/level_h/btt_sensor.md

Closed 2025-02-05.

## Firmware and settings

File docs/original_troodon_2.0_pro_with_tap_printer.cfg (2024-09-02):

#370021001047323237363638# This file contains common pin mappings for the BigTreeTech Octopus X7
# To use this config, the firmware should be compiled for the STM32F407 with a "32KiB bootloader"

# after running "make", copy the generated "klipper/out/klipper.bin" file to a
# file named "firmware.bin" on an SD card and then restart the OctoPus with that SD card.

# See docs/Config_Reference.md for a description of parameters.

## Formbot / Vivedino Troodon 2.0
## Firmware Version: 1.2
## Compiled By: YGK3D
## Release Date: 02/09/23

## *** THINGS TO CHANGE/CHECK: ***
## MCU paths                            [mcu] section
## Thermistor types                     [extruder] and [heater_bed] sections - See https://www.klipper3d.org/Config_Reference.html#common-thermistors for common thermistor types
## Z Endstop Switch location            [safe_z_home] section
## Homing end position                  [gcode_macro G32] section
## Z Endstop Switch  offset for Z0      [stepper_z] section
## Probe points                         [quad_gantry_level] section
## Min & Max gantry corner postions     [quad_gantry_level] section
## PID tune                             [extruder] and [heater_bed] sections
## Probe pin                            [probe] section
## Fine tune E steps                    [extruder] section

[include mainsail.cfg]

[mcu]
##  Obtain definition by "ls -l /dev/serial/by-id/" then unplug to verify
##--------------------------------------------------------------------
serial: /dev/serial/by-id/usb-Klipper_stm32f407xx_3B001F001647323137363638-if00
restart_method: command
##--------------------------------------------------------------------

[printer]
kinematics: corexy
max_velocity: 300  
max_accel: 3000             #Max 4000
max_z_velocity: 15          #Max 15 for 12V TMC Drivers, can increase for 24V
max_z_accel: 350
square_corner_velocity: 5.0

#####################################################################
#   X/Y Stepper Settings
#####################################################################

##  B Stepper - Left
##  Connected to MOTOR_0
##  Endstop connected to DIAG_0
[stepper_x]
step_pin: PA3
dir_pin: PA4
enable_pin: !PA1
rotation_distance: 40
microsteps: 32
full_steps_per_rotation:200  #set to 400 for 0.9 degree stepper
endstop_pin: PF2
position_min: 0
##--------------------------------------------------------------------

##  Uncomment below for 250mm build
#position_endstop: 250
#position_max: 250

##  Uncomment for 300mm build
#position_endstop: 300
#position_max: 300

##  Uncomment for 350mm build
position_endstop: 350
position_max: 350

##--------------------------------------------------------------------
homing_speed: 50   #Max 100
homing_retract_dist: 5
homing_positive_dir: true

##  Make sure to update below for your relevant driver (2208 or 2209)
[tmc2209 stepper_x]
uart_pin: PA2
interpolate: false
run_current: 0.8
sense_resistor: 0.110
stealthchop_threshold: 0

##  A Stepper - Right
##  Connected to MOTOR_1
##  Endstop connected to DIAG_1
[stepper_y]
step_pin: PC2
dir_pin: PC3
enable_pin: !PC1
rotation_distance: 40
microsteps: 32
full_steps_per_rotation:200  #set to 400 for 0.9 degree stepper
endstop_pin: PC15
position_min: 0
##--------------------------------------------------------------------

##  Uncomment for 250mm build
#position_endstop: 250
#position_max: 250

##  Uncomment for 300mm build
#position_endstop: 300
#position_max: 300

##  Uncomment for 350mm build
position_endstop: 355
position_max: 355

##--------------------------------------------------------------------
homing_speed: 50  #Max 100
homing_retract_dist: 5
homing_positive_dir: true

##  Make sure to update below for your relevant driver (2208 or 2209)
[tmc2209 stepper_y]
uart_pin: PC0
interpolate: false
run_current: 0.8
sense_resistor: 0.110
stealthchop_threshold: 0
 
#####################################################################
#   Z Stepper Settings
#####################################################################

## Z0 Stepper - Front Left
##  Connected to MOTOR_4
##  Endstop connected to DIAG_4
[stepper_z]
step_pin: PB10
dir_pin: PB11
enable_pin: !PE15
rotation_distance: 40
gear_ratio: 80:16
microsteps: 32
#endstop_pin: PF4
endstop_pin:probe:z_virtual_endstop
##  Z-position of nozzle (in mm) to z-endstop trigger point relative to print surface (Z0)
##  (+) value = endstop above Z0, (-) value = endstop below
##  Increasing position_endstop brings nozzle closer to the bed
##  After you run Z_ENDSTOP_CALIBRATE, position_endstop will be stored at the very end of your config
#position_endstop: 0
##--------------------------------------------------------------------

##  Uncomment below for 250mm build
#position_max: 210

##  Uncomment below for 300mm build
#position_max: 260

##  Uncomment below for 350mm build
position_max: 310

##--------------------------------------------------------------------
position_min: -5
homing_speed: 8
second_homing_speed: 3
homing_retract_dist: 3

##  Make sure to update below for your relevant driver (2208 or 2209)
[tmc2209 stepper_z]
uart_pin: PE14
interpolate: false
run_current: 0.8
sense_resistor: 0.110
stealthchop_threshold: 0

##  Z1 Stepper - Rear Left
##  Connected to MOTOR_3
[stepper_z1]
step_pin: PE11
dir_pin: !PE12
enable_pin: !PE10
rotation_distance: 40
gear_ratio: 80:16
microsteps: 32

##  Make sure to update below for your relevant driver (2208 or 2209)
[tmc2209 stepper_z1]
uart_pin: PE9
interpolate: false
run_current: 0.8
sense_resistor: 0.110
stealthchop_threshold: 0

##  Z2 Stepper - Rear Right
##  Connected to MOTOR_6
[stepper_z2]
step_pin: PE7
dir_pin: PE8
enable_pin: !PG1
rotation_distance: 40
gear_ratio: 80:16
microsteps: 32

##  Make sure to update below for your relevant driver (2208 or 2209)
[tmc2209 stepper_z2]
uart_pin: PG0
interpolate: false
run_current: 0.8
sense_resistor: 0.110
stealthchop_threshold: 0

##  Z3 Stepper - Front Right
##  Connected to MOTOR_5
[stepper_z3]
step_pin: PF13
dir_pin: !PF14
enable_pin: !PF12
rotation_distance: 40
gear_ratio: 80:16
microsteps: 32

##  Make sure to update below for your relevant driver (2208 or 2209)
[tmc2209 stepper_z3]
uart_pin: PF11
interpolate: false
run_current: 0.8
sense_resistor: 0.110
stealthchop_threshold: 0


#####################################################################
#   Extruder
#####################################################################

##  Connected to MOTOR_2
##  Heater - HE0
##  Thermistor - T0
[extruder]
step_pin: PB0
dir_pin: PB1
enable_pin: !PC5
##  Update value below when you perform extruder calibration
##  If you ask for 100mm of filament, but in reality it is 98mm:
##  rotation_distance = <previous_rotation_distance> * <actual_extrude_distance> / 100
##  22.6789511 is a good starting point
rotation_distance: 22.6789511   #Bondtech 5mm Drive Gears
##  Update Gear Ratio depending on your Extruder Type
##  Use 50:10 for Stealthburner/Clockwork 2
##  Use 50:17 for Afterburner/Clockwork (BMG Gear Ratio)
##  Use 80:20 for M4, M3.1
gear_ratio: 50:10               #BMG Gear Ratio
microsteps: 32
full_steps_per_rotation: 200    #200 for 1.8 degree, 400 for 0.9 degree
nozzle_diameter: 0.400
filament_diameter: 1.75
heater_pin: PB9
## Check what thermistor type you have. See https://www.klipper3d.org/Config_Reference.html#common-thermistors for common thermistor types.
## Use "Generic 3950" for NTC 100k 3950 thermistors
sensor_type: PT1000
sensor_pin: PF3
min_temp: 0
max_temp: 500
max_power: 1.0
min_extrude_temp: 170
max_extrude_only_distance: 150
control = pid
pid_kp = 26.213
pid_ki = 1.304
pid_kd = 131.721
##  Try to keep pressure_advance below 1.0
#pressure_advance: 0.05
##  Default is 0.040, leave stock
#pressure_advance_smooth_time: 0.040

##  E0 on MOTOR_2
##  Make sure to update below for your relevant driver (2208 or 2209)
[tmc2209 extruder]
uart_pin: PC4
interpolate: false
run_current: 0.5
sense_resistor: 0.110
stealthchop_threshold: 0


#####################################################################
#   Bed Heater
#####################################################################

##  SSR Pin - HE1
##  Thermistor - TB
[heater_bed]
##  Uncomment the following line if using the default SSR wiring from the docs site
#heater_pin: PA3
##  Other wiring guides may use BED_OUT to control the SSR. Uncomment the following line for those cases
heater_pin: PD12
## Check what thermistor type you have. See https://www.klipper3d.org/Config_Reference.html#common-thermistors for common thermistor types.
## Use "Generic 3950" for Keenovo heaters
sensor_type: Generic 3950
sensor_pin: PA0
##  Adjust Max Power so your heater doesn't warp your bed. Rule of thumb is 0.4 watts / cm^2 .
max_power: 0.6
min_temp: 0
max_temp: 120
control: pid
pid_kp: 58.437
pid_ki: 2.347
pid_kd: 363.769

#####################################################################
#   Probe
#####################################################################
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

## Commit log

2024-05-28 Update and rename docs/level_m/TIMER.md to macros/TIMER.md
2024-05-29 Update and rename CANCEL_PRINT.md to PRINT_CANCEL.md
2024-06-17 Rename Troodon_Alignment_Bracket.stl to 3D files/Troodon_Alignment_Bracket.stl
    [Troodon_Alignment_Bracket.stl]
2024-08-24 Add The Rear Panel section
    [Back Panel Inserts-SideBottom.3mf, Back Panel Inserts-SideMiddle.3mf, Back Panel Inserts-TopLeft.3mf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]
2024-08-24 Rename Back Panel Inserts-SideBottom.3mf to Back_Panel_Inserts-SideBottom.3mf
    [Back_Panel_Inserts-SideBottom.3mf]
2024-08-24 Rename Back Panel Inserts-SideMiddle.3mf to Back_Panel_Inserts-SideMiddle.3mf
    [Back_Panel_Inserts-SideMiddle.3mf]
2024-08-24 Rename Back Panel Inserts-TopLeft.3mf to Back_Panel_Inserts-TopLeft.3mf
    [Back_Panel_Inserts-TopLeft.3mf]
2024-08-24 Rename Back Panel Inserts-TopMiddle.3mf to Back_Panel_Inserts-TopMiddle.3mf
    [Back_Panel_Inserts-TopMiddle.3mf]
2024-08-24 Rename Back Panel Inserts-TopRight.3mf to Back_Panel_Inserts-TopRight.3mf
    [Back_Panel_Inserts-TopRight.3mf]
2024-09-02 Rename original troodon 2.0 pro with tap printer.cfg to original_troodon_2.0_pro_with_tap_printer.cfg
    [original_troodon_2.0_pro_with_tap_printer.cfg]
